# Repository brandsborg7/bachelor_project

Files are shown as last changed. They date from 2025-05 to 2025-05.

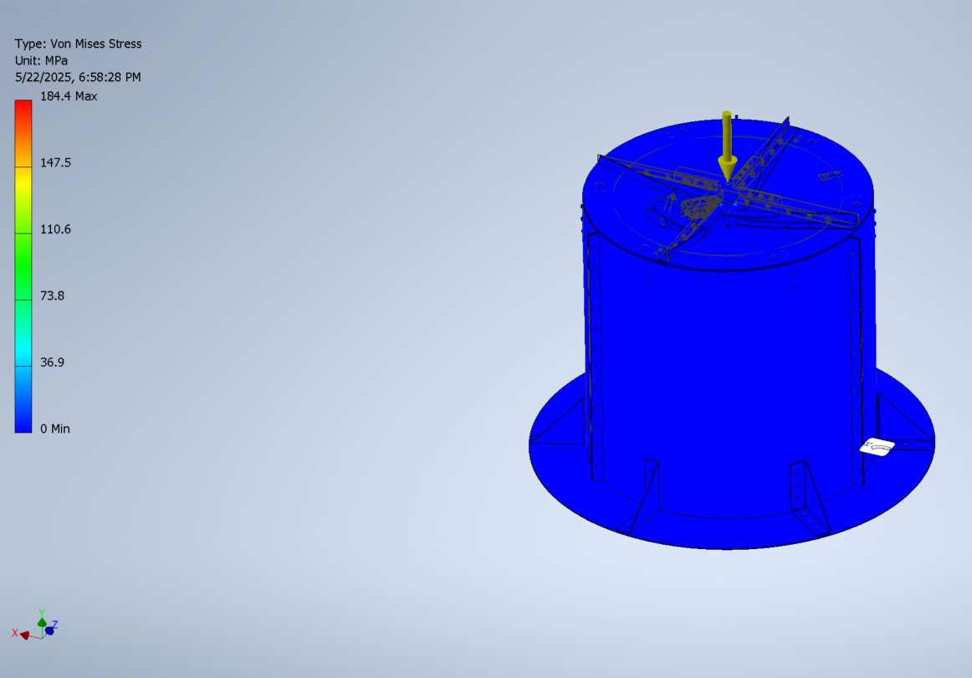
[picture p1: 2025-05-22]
CAD-files/FEA_chamber_results.png

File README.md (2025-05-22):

# bachelor_project
All codes from the workspace on the Raspberry PI of our bachelor project 
NB! Not in the exact way they are represented in the workspace folder on the RPi, but just to illustrate all the codes 
the most efficient way (for the bachelor report) 

Each node-folder has a package.xml, setup.py (used for building the package), as well as the Python code for the node. 

Extra files included: 
- logfile (from last final testings 19th of May)
- Plots/graphs from the sensor data (created by the logger_node as .png files)
- dockerfile.txt & docker-compose.yml (used to create, build & run the Docker environment)
- config.txt file (which is the config file for the Raspberry Pi located in /boot/firmware/config.txt)

Additional: 
- The project's BOM list is included (BOM_våk_field_flux.xlsx)
- All CAD-files (technical drawings) are in the CAD-files folder

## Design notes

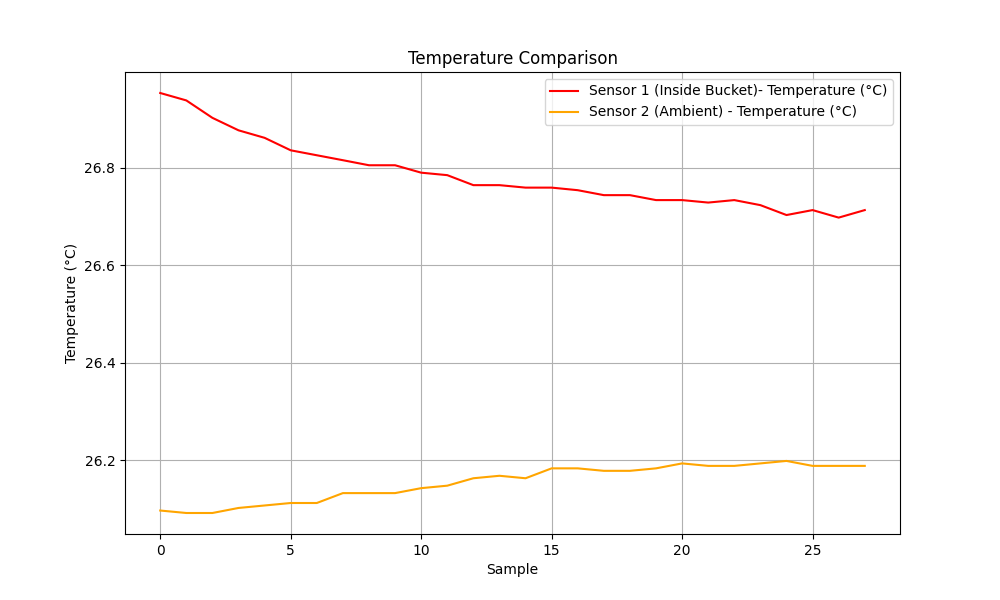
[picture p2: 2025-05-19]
Plots (sensor data)/19.mai/temperature_comparison_2025-05-19_14-41-35.png

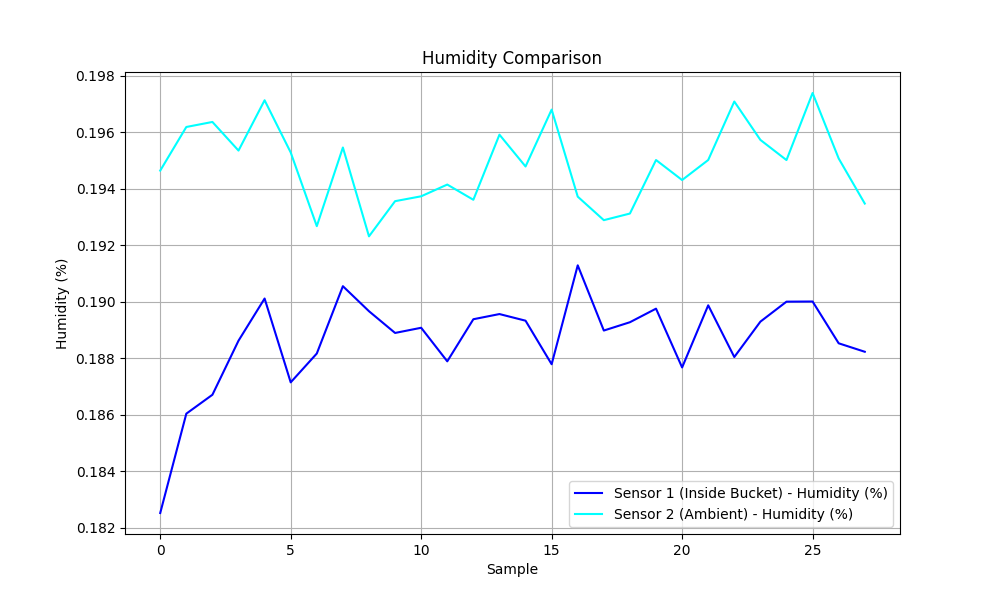
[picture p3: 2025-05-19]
Plots (sensor data)/19.mai/humidity_comparison_2025-05-19_14-41-35.png

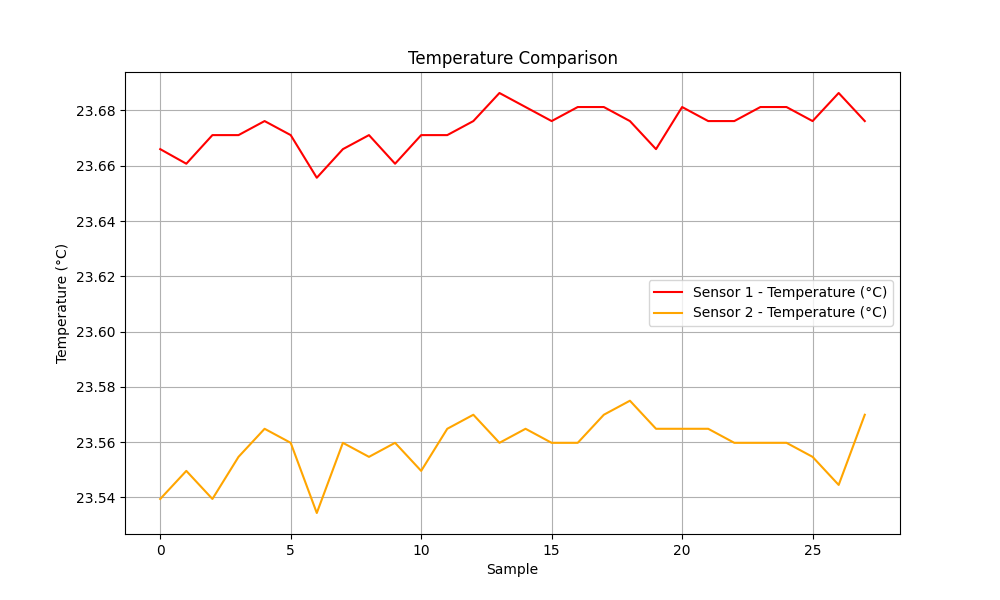
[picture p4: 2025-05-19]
Plots (sensor data)/16.mai/temperature_comparison_2025-05-16_08-13-00.png

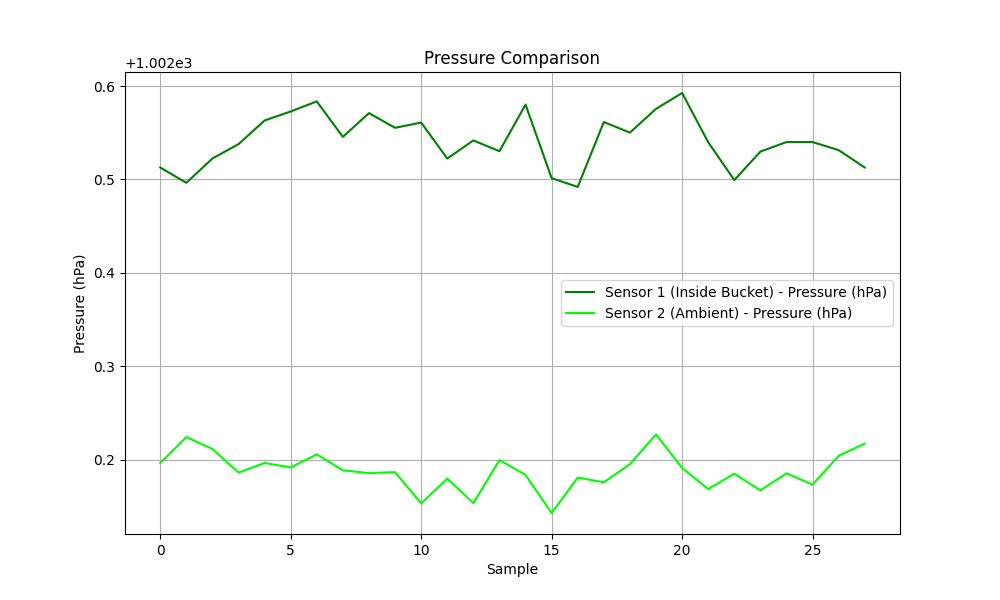
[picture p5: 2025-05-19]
Plots (sensor data)/19.mai/pressure_comparison_2025-05-19_14-41-35.png

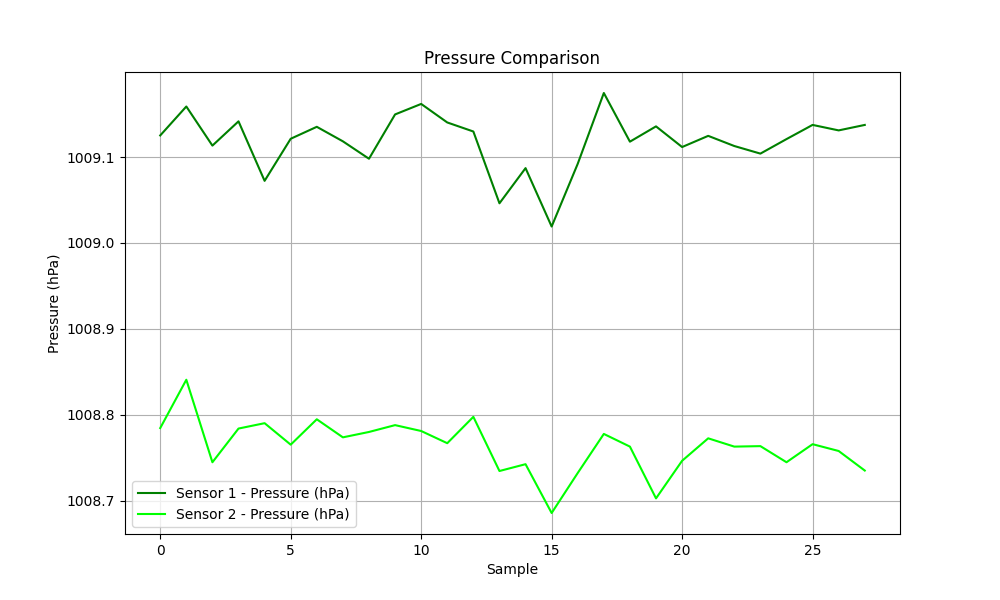
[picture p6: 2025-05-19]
Plots (sensor data)/16.mai/pressure_comparison_2025-05-16_08-13-00.png

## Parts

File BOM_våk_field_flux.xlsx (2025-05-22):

BOM (Bill of Materials)
Electronics / hardware | Quantity | Category | Description / Specifications | Notes | Source / Link
Raspberry Pi 5 | 2 | RPi |  |  | https://no.farnell.com/raspberry-pi/rpi5-4gb-single/raspberry-pi-5-model-b-4gb-2-4ghz/dp/4255998
Rasperry PI case w/cooling fan | 2 | RPi | Protective case w/cooling fan for the RPi 5 |  | https://no.farnell.com/raspberry-pi/sc1160/case-raspberry-pi-5-model-b-plastic/dp/4263048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
Storage: MicroSD m/adapter | 2 | RPi | 128 GB |  | https://no.farnell.com/hama/00124160/128gb-c10-uhs-i-microsdhc-80mb/dp/3410186
Rasperry Pi Power Supply | 1 | RPi | 5V, USB-C |  | https://no.farnell.com/raspberry-pi/sc1152/power-supply-usb-c-5-1v-5a-white/dp/4263039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
Rasperry Pi Motor Driver Board | 1 | RPi | 4A, 24V |  | https://thepihut.com/products/raspberry-pi-motor-driver-board
24V Battery (Power source) | 1 | Power |  | Ended up using the battery already installed in VÅK | Adigo
Mikroswitch (endebryter) | 2 |  |  | Did not end up using them | https://no.farnell.com/omron/z-15g/microswitch-spdt-15a-250vac-solder/dp/3413281 | https://no.mouser.com/ProductDetail/Saia-Burgess/XGC2-88Z1?qs=lDMevKbHVys%2F1Eo18luQHQ%3D%3D | https://no.rs-online.com/web/p/micro-switches/8046225?gb=s
RC Servo | 2 | Bøtte | To open & close lids of bucket |  | https://www.elefun.no/vare-1016/radioutstyr-servo-hitec-hs-322hd
Voltage Regulator | 1 | Power | Step down 24V to 5V (5A output) | Ended up using the voltage regulator already installed the VÅK | https://no.farnell.com/mean-well/sd-25a-5/dc-dc-converter-5v-5a/dp/2816175
Voltage Regulator (VÅK) | 1 | Power | Step down 24V to 5V (5A output) |  | Adigo
Ethernet cable | 2 | Wiring | CAT6 |  | Adigo
DC Axial-fan | 2 | Bøtte | 40 x 40mm, 5V |  | https://no.farnell.com/sepa/lf40p05pse00a/dc-fan-40mm-7500rpm-5v-0-1a/dp/3886338
USB HD-Camera | 2 | Bøtte | 41 mm x 41 mm x 41.5 mm, 5V, 1080p Full HD |  | https://no.mouser.com/ProductDetail/AAEON-UP/EP-DCOV2735-F36?qs=w%2Fv1CP2dgqpCcX2%252BgWo9%2Fg%3D%3D
Male USB A to Female USB A | 2 | Wiring | 480Mbps, 1.8m |  | https://no.rs-online.com/web/p/usb-cables/1862790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
Wires |  | Wiring | 18-22 AWG |  | Adigo
Environmental Sensor | 2 | Bøtte | I2C: temperature, humidity, pressure |  | https://no.farnell.com/en-NO/seeed-studio/101020193/sensor-board-arduino-board/dp/3932095?cfm=true
Våk-robot | 1 |  |  |  | Adigo
Mechanical parts | Quantity | Category | Description / Specifications | Notes | Source / Link
Aluminium til bom | 1 | Bom | 210cm x 4cm x 3cm | Al rør rektang 6060-T6 60x40x3mm a 6000mm (vi trenger totalt 350cm) | Astrup.no
Aluminium til bom | 1 | Bom | 110cm x 4cm x 3cm | Al rør rektang 6060-T6 60x40x3mm a 6000mm (vi trenger totalt 350cm) | Astrup.no
1m aluminiumsrør | 1 | Kobling | 6060-T6 22x2mm | Al rør 6060-T6 22x2mm a 6000mm | Astrup.no
1m aluminiumsrør | 1 | Kobling | 6060-T6 35x2mm | Al rør 6060-T6 35x2mm a 6000mm | Astrup.no
Aluminium-plater | 2 | Bøtte | 2m x 1m x 2mm |  | Astrup.no
Alu vinkelprofil | 1 | Bøtte | 6m (20 x 20 x 2mm) | https://kundeportal.astrup.no/aluminium/alu-vinkler-like-ulikebent | Astrup.no
Wire til festet på bøtta | 1 | Kobling | 3m x 2mm |  | RS PRO Galvanised Metal Wire Rope, 50m | RS (https://no.rs-online.com/web/p/rope/1244758)
3D-print bushing | 4 | Kobling |  |  | Adigo
Clamping knob (til bøtter) | 2 | Bøtte |  |  | RS PRO Clamping Lever, M8 x 40mm | RS (https://no.rs-online.com/web/p/clamping-levers/0478945?matchtype=&gad_source=1&gclsrc=aw.ds)
rivets, aluminium | 3 pcs of 50 units | Bøtte | 5mm |  | RS PRO Aluminium Blind Rivet, 4.8mm | RS (https://no.rs-online.com/web/p/rivets/2065416?gb=a)
Luftslange kobling (siste fase av produksjon) | 2 | Bøtte |  |  | RS PRO Straight Tube-to-Tube Adaptor, Push In 6 mm to Push In 6 mm, Tube-to-Tube Connection Style | RS (https://no.rs-online.com/web/p/pneumatic-fittings/9160873)
Vakuumslange (siste fase av produksjon) |  | Bøtte | 8m x 6mm |  | https://no.rs-online.com/web/p/hose-pipe-flexible-tubes/9145515?gb=s
Endeledd | 2 | Bøtte | M6 45mm |  | RS PRO M6 x 1 Male Steel Rod End, 6mm Bore, 45mm Long, Metric Thread Standard, Male Connection Gender | RS (https://no.rs-online.com/web/p/rod-ends/1989077?gb=s)
Gassfjær 6-15 | 2 | Kobling | 200mm strokelength - Total length: 430 +/- 2mm, 150N |  | Gassfjær 4-12 - slaglengde 150 - Gassfjaershop.no (https://www.gassfjaershop.no/produkt/gassfjaer-4-12-slaglengde-150/)
Neopren | 1 | Bøtte | 1m x 0,6m x 1,5mm |  | Rubber Sheets | RS (https://no.rs-online.com/web/c/engineering-materials-industrial-hardware/plastic-rubber-materials/rubber-sheets/)
M8 theaded insert diameter | 4 | Bøtte | 11mm |  | PSZFON-0830 | POP Steel Tubular Rivet, 10.9mm, M8 thread | RS (https://no.rs-online.com/web/p/rivets/7689984?gb=s)
M5 threaded insert diameter | 8 | Bøtte | 7mm |  | RS PRO Black Multiple Lobes Clamping Knob, M8, Threaded Stud | RS (https://no.rs-online.com/web/p/clamping-knobs/7027633)
Foam | 1 | Bøtte | 10 x 6 x 5000 mm |  | Adigo
Bøjlewirelås DIN741 |  |  | A2 2 mm |  | https://www.globaltools.no/tekniske-artikler/wire-kaeder/-7854/wireklemme-alu-z-20-mm-100-stk
Trådklemme alu-z |  |  | 2,0 mm |  | https://www.globaltools.no/tekniske-artikler/wire-kaeder/-7854/bojlewirelas-din741-a2-2-mm
Poppnagler | 150 |  | 4,8x10 "plain" alu
Source / suppliers:
Astrup.no
Norsk stål
Tverlie sveis (vals og tig)
Takshop.no (vals og tig)
no.farnell.com
https://no.rs-online.com/web/
https://no.farnell.com/
Global Tools
www.gassfjaershop.no

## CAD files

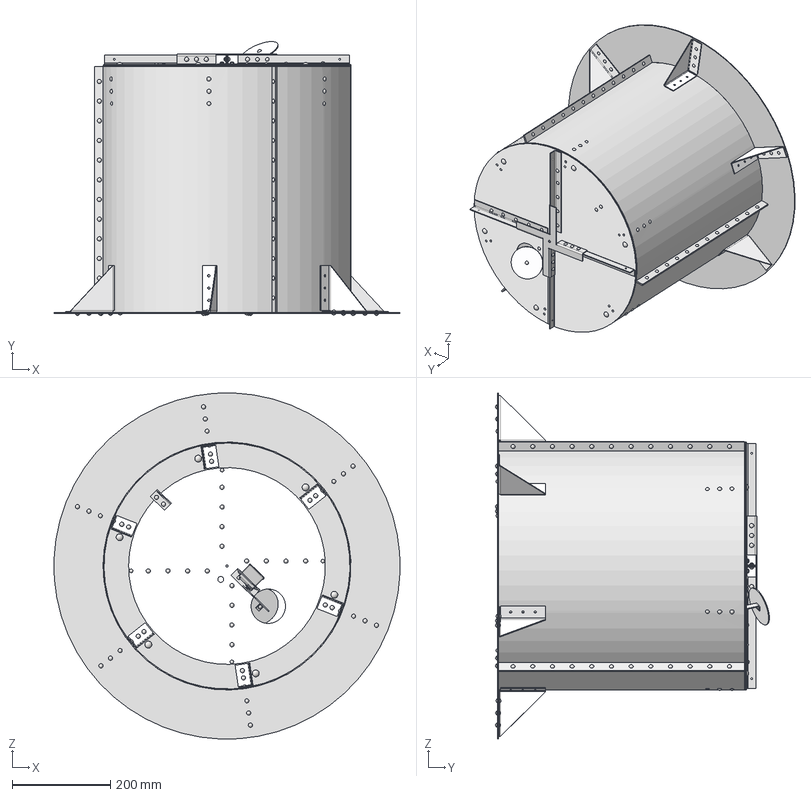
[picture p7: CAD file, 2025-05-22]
CAD-files/assembly_lokk.stp
703.4 x 556.9 x 703.4 mm
Lokk_strut x 4
connector_cross
lufte_lokk
lokk
servofeste
servo_arm
vifte
_HS-322HD
ISO/R 1051 - 5 x 10 x 121
botte_sylinder_tredelt x 3
botte_kant
botte_skjort
botte_skjort_feste x 6
botte_kant_feste x 6
ISO/R 1051 - 8 x 14 x 6

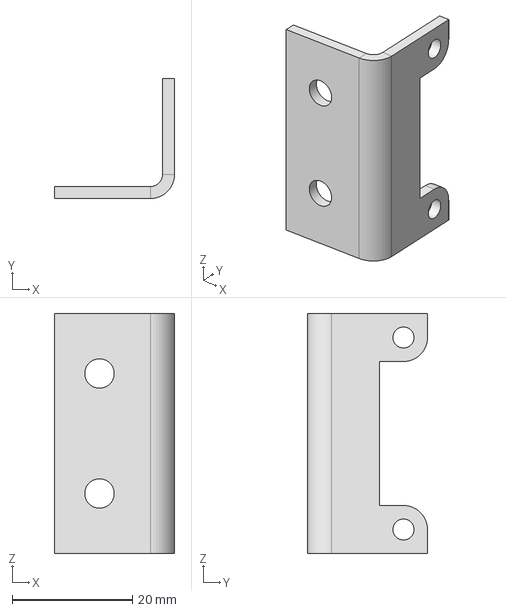
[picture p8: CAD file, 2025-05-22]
CAD-files/vifte.stp
20.0 x 20.0 x 40.0 mm

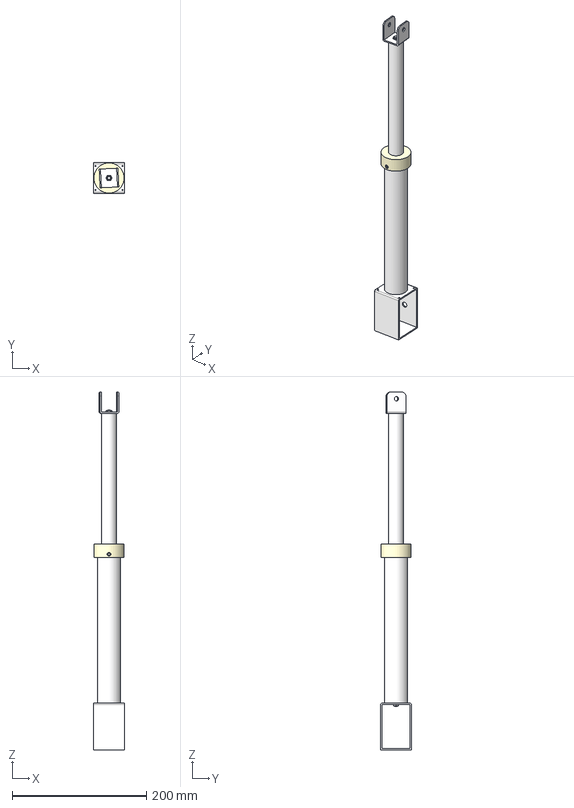
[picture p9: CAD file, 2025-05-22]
CAD-files/Piston damper.stp
46.0 x 46.0 x 534.0 mm
Bushing outer
Ny type indre
Øvre del kobling
Bushing indre kobling
ISO 1207 - M3 x 4 x 2
rod
thread rod
thread cylinder
ISO 4035 - M5 x 2
ISO 1207 - M2,5 x 3 x 2

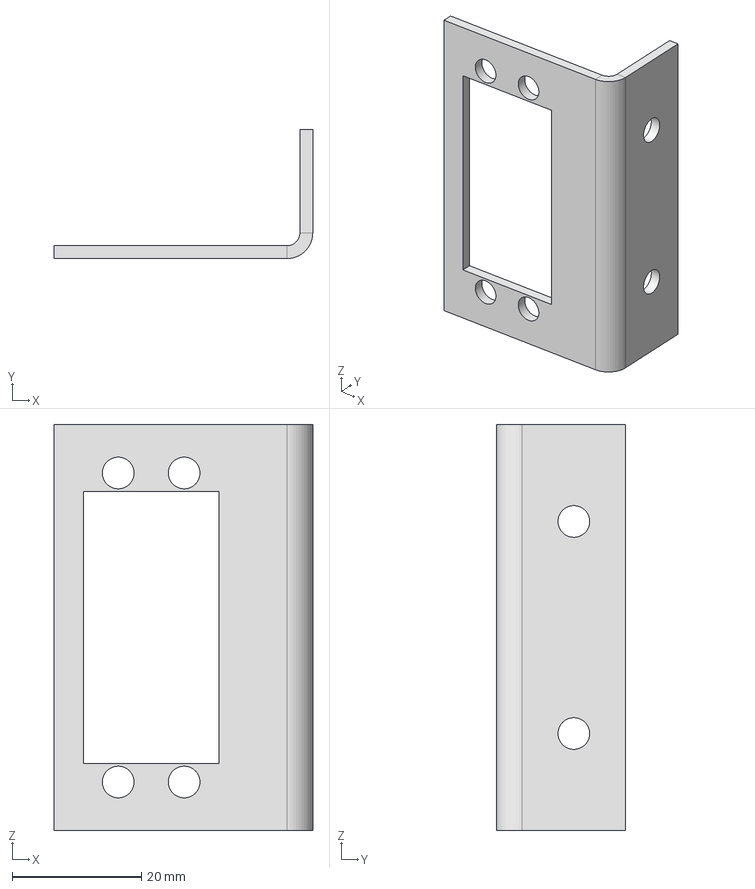
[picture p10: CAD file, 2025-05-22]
CAD-files/servofeste.stp
40.0 x 20.0 x 62.8 mm

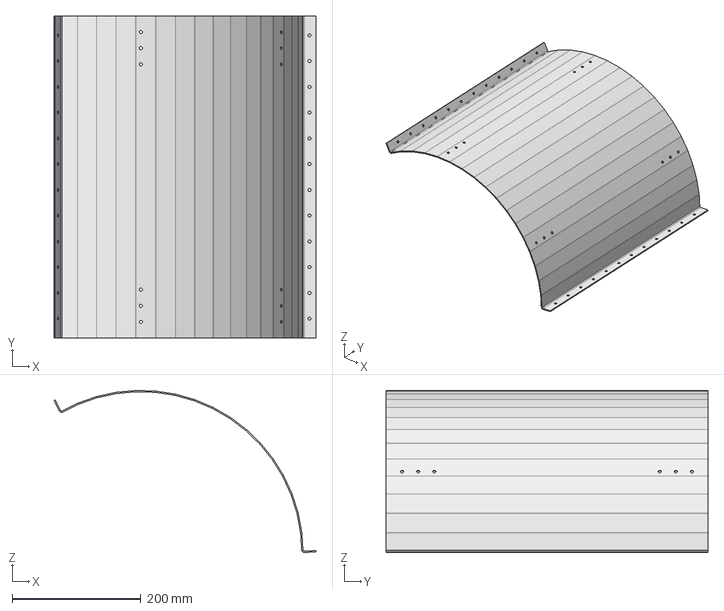
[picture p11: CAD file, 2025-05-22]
CAD-files/botte_sylinder_tredelt_sheet.stp
406.8 x 500.0 x 251.6 mm

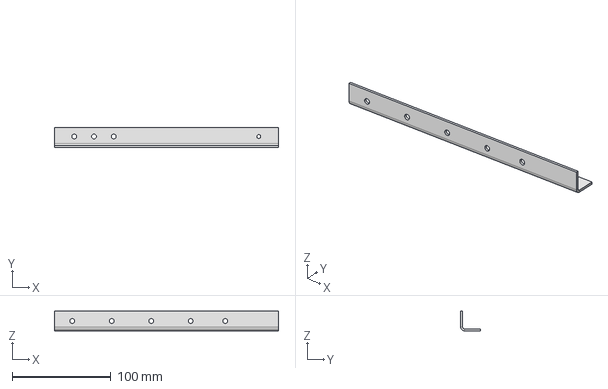
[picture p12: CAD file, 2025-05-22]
CAD-files/Lokk_strut.stp
227.0 x 20.0 x 20.0 mm

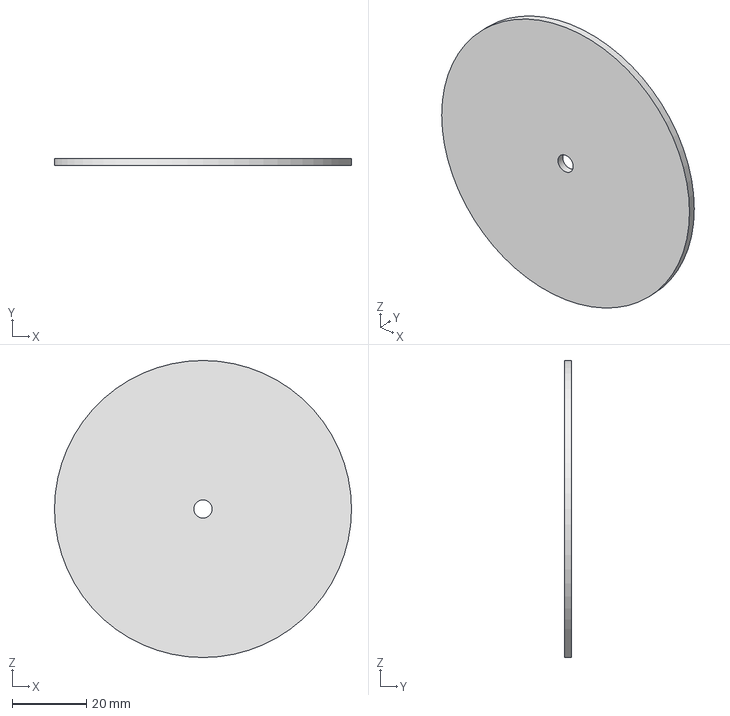
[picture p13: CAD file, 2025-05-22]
CAD-files/lufte_lokk.stp
80.0 x 2.00 x 80.0 mm

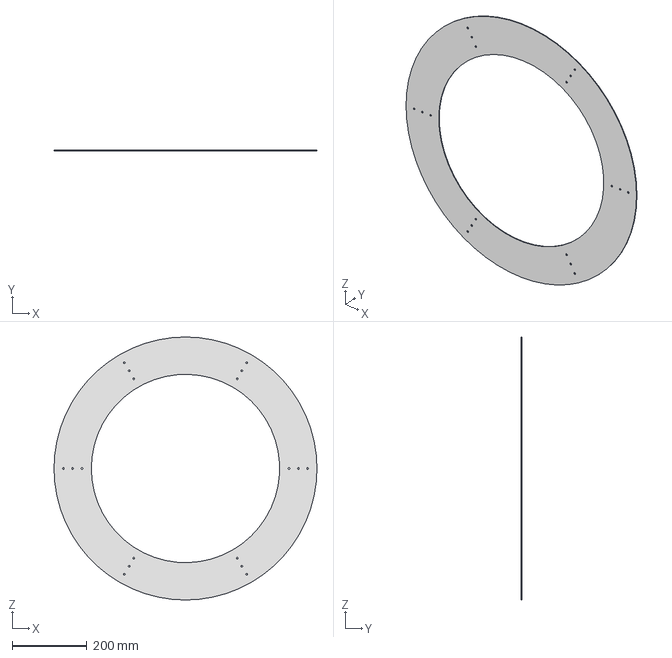
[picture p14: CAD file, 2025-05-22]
CAD-files/botte_skjort.stp
704.0 x 2.00 x 704.0 mm

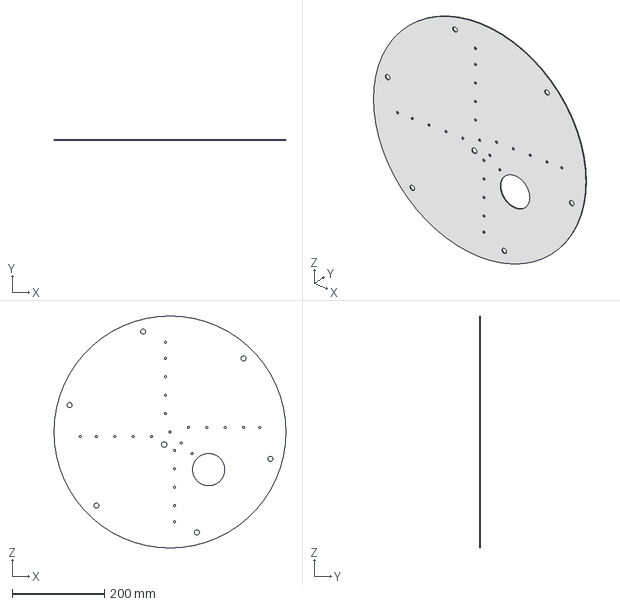
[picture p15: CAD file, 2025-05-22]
CAD-files/lokk.stp
504.0 x 2.00 x 504.0 mm

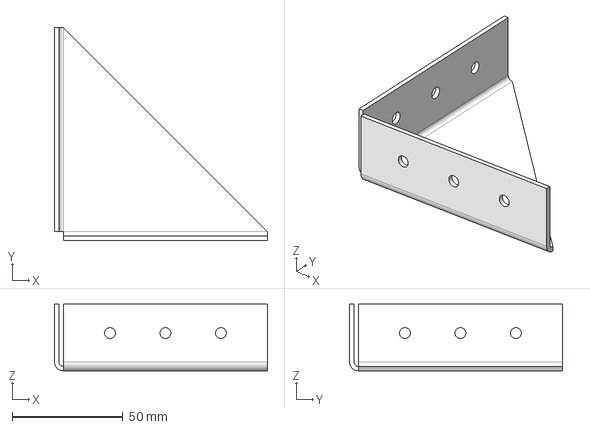
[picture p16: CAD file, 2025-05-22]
CAD-files/botte_skjort_feste.stp
96.0 x 96.0 x 30.0 mm

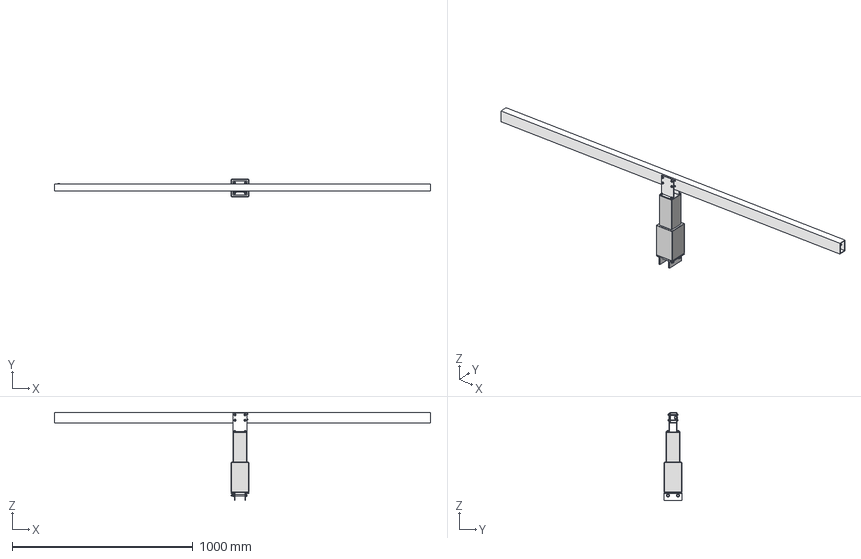
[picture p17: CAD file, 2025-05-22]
CAD-files/Beam and brackets simple.stp
2080.0 x 97.0 x 489.2 mm
Bom_simple
Heis dummy nedre stilling
ISO 7091 - ST 8 - 100 HV x 2
ISO 4034 - M8 x 2
ISO 4762 - M5 x 25 x 4
ISO 4162 - M5 x 50 x 4
ISO 4161 - M5 x 4
Nut GB/T 17880.4-1999 M8 x 15 x 2
Brakett nedre x 2
ISO 4162 - M8 x 80 x 2
Bom brakett øvre x 2

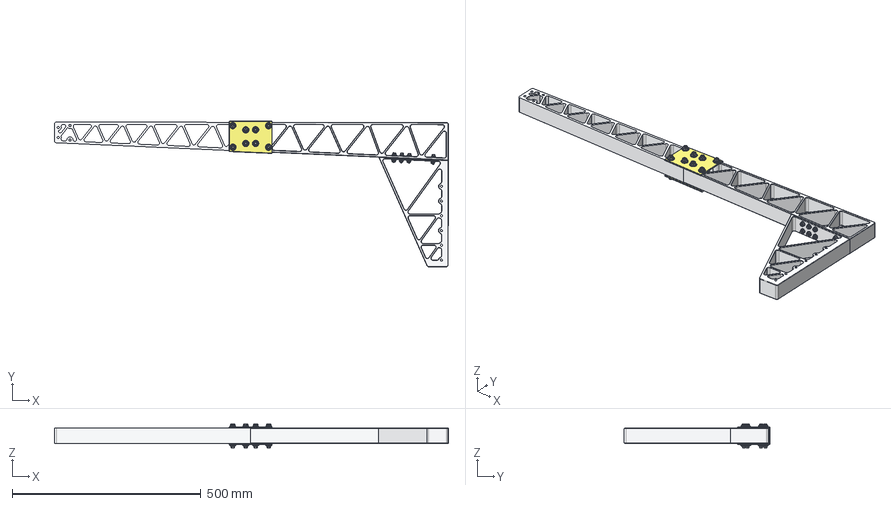
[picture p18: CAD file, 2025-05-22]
CAD-files/Framework.stp
1042.5 x 385.6 x 63.2 mm
Bom_fag_øvre
Bom_fag_nedre
IFI - 5, RTW x 16
IFI 502 - M5x0,8 x 20, HFHTSTDM x 8
ANSI B18.2.4.4M - M5 x 0,8 x 8
Bom_brakett
IFI - 6, RTW x 16
IFI 536 - M6x1 x 55, HFSM x 8
ANSI B18.2.4.4M - M6 x 1 x 8

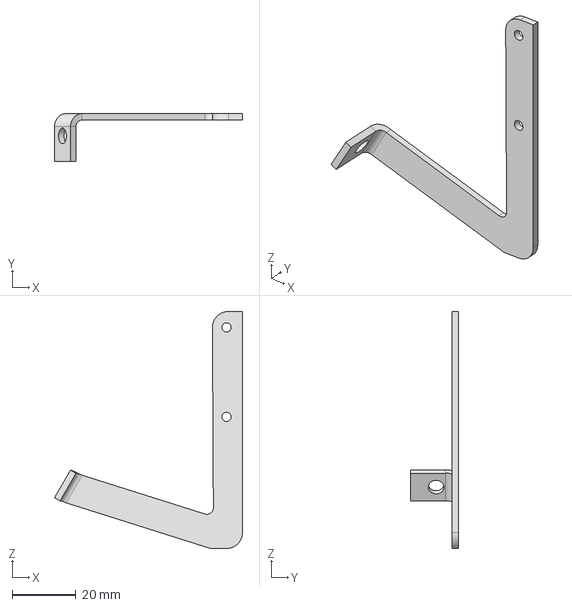
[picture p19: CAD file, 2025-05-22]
CAD-files/servo_arm.stp
58.9 x 15.0 x 74.2 mm

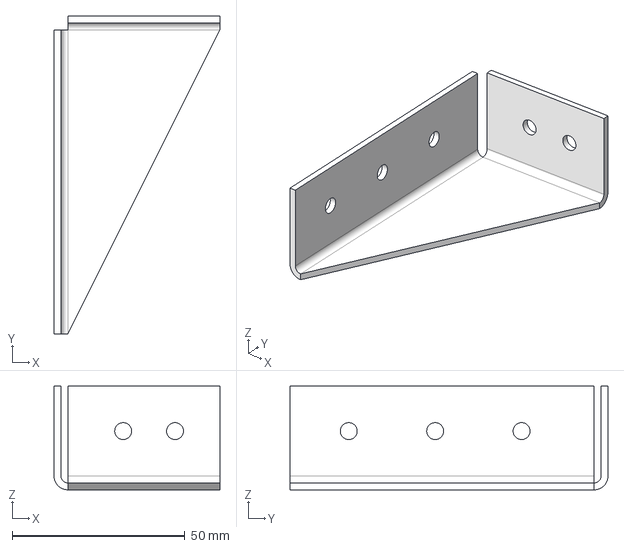
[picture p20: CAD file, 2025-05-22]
CAD-files/botte_kant_feste.stp
48.0 x 92.0 x 30.0 mm

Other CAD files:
CAD-files/connector_cross.stp
CAD-files/botte_kant.stp

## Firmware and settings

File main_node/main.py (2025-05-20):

import rclpy
from rclpy.node import Node
from rclpy.executors import MultiThreadedExecutor
from std_msgs.msg import String
import time
import threading

# Importing necessary modules for the main node
from lift_node.lift import LiftNode
from sensor_node.sensor import SensorPublisher
from rc_servo_node.rc_servo import RCServoNode
from fan_node.fan import FanNode
from camera_node.camera import CameraNode

class MainNode(Node):
    def __init__(self):
        super().__init__('main_node')

        # Log the node startup using ROS 2 logger
        self.get_logger().info("Main Node has been started")

        # Initial variable conditions
        self.running = True
        self.shutdown_everything = False
        self.lift_in_stopped_condition = True
        self.lift_sequence_phase = None
        self.sequence_active = False

        # Initialize the nodes (with error handling)
        self.lift_node = self.safe_init(LiftNode)
        self.sensor_node = self.safe_init(SensorPublisher)  
        self.rc_servo_node = self.safe_init(RCServoNode)
        self.fan_node = self.safe_init(FanNode)
        self.camera1_node = self.safe_init(CameraNode, 0)
        self.camera2_node = self.safe_init(CameraNode, 2)
        
        # Publishers
        self.lift_cmd_publisher = self.create_publisher(String, 'lift_cmd', 10) # lift_cmd topic
        self.shutdown_pub = self.create_publisher(String, 'shutdown_topic', 10) # shutdown_topic

        # Lift status subscriber (for sequence control)
        self.lift_status_sub = self.create_subscription(String, 'lift_status', self.lift_status_callback, 10)

    # Function to safely initialize nodes (w/its arguments and keyword-arguments) and handle exceptions
    def safe_init(self, class_name, *args, **kwargs):
        try:
            return class_name(*args, **kwargs)
        except Exception as e:
            self.get_logger().error(f"Failed to initialize {class_name.__name__}: {e}")
            return None

    # Function to send shutdown message to the logger node
    def shutdown_logger(self):
        msg = String()
        msg.data = 'shutdown'
        self.shutdown_pub.publish(msg)
        self.get_logger().info('Sendt shutdown message to logger_node.')

    def send_lift_command(self, command: str):
        try:
            msg = String()
            msg.data = command
            self.lift_cmd_publisher.publish(msg)
            self.get_logger().info(f"Sent command: {command}")
        except Exception as e:
            self.get_logger().error(f"Failed to send lift command: {e}, command: {command}")

    def shutdown_nodes(self):

        # Stop the command loop
        self.running = False

        nodes_to_shutdown = [
            self.lift_node,
            self.sensor_node,
            self.rc_servo_node,
            self.fan_node,
            self.camera1_node,
            self.camera2_node,
        ]

        for node in nodes_to_shutdown:
            if node:
                try:
                    node_name = node.get_name()
                    node.destroy_node()
                    self.get_logger().info(f"Node {node_name} has been destroyed.")
                except Exception as e:
                    self.get_logger().error(f"Failed to destroy node: {e}")
            else:
                self.get_logger().warn("Node is None, skipping destruction.")
        
        self.get_logger().info("Main node shutting down.")

    # Function to start multiple threads simultaneously (just starting them)
    def start_threads(self, funcs):
        threads = []
        for f in funcs:
            thread = threading.Thread(target=f)
            thread.start()
            threads.append(thread)
        return threads
    
    def run_thread_and_wait(self, funcs):
        threads = self.start_threads(funcs)
        for thread in threads:
            thread.join()

    def lift_status_callback(self, msg):
        status = msg.data
        self.get_logger().info(f"Received lift status: {status}")

        # Only handle lift status when in full sequence
        if not self.sequence_active:
            return

        if status == "Lift stopped":

            # Step 5: Close the LIDs (servos), turn off fans 
            if self.sequence_phase == 1:   # Lift down just finished (STOPPED)
                

                if self.rc_servo_node:
                    self.run_thread_and_wait([
                    lambda: self.rc_servo_node.servo_1.process_command("close"),
                    lambda: self.rc_servo_node.servo_2.process_command("close"),
            ])

                self.get_logger().info("Lift down completed. Closing servos.")
                
                self.get_logger().info("Servos closed. Turning off fans.")
                self.fan_node.turn_off_fans()

                # Step 6: Lift up
                if self.lift_node:
                    self.lift_node.lift_up(duration=40)
                self.sequence_phase = 2

            # Step 7 (final): stop the sequence & turn off cameras
            elif self.sequence_phase == 2:  # Lift up just finished (STOPPED)
                # Lift up just finished
                self.get_logger().info("Lift up completed. Turning off cameras")
                
                # Stop the cameras 
                for thread in self.camera_threads:
                    thread.join()

                self.lift_in_stopped_condition = True
                self.sequence_phase = None
                self.sequence_active = False 
                self.get_logger().info("Full sequence completed.")

    def full_sequence(self): 
        self.get_logger().info("Starting full sequence...")

        if not all([self.lift_node, self.fan_node, self.rc_servo_node]):
            self.get_logger().error("❌ One or more required nodes are not initialized. Aborting sequence.")
            return

        if not self.lift_in_stopped_condition:
            self.get_logger().warn("⚠️ Lift is currently moving. Wait for it to stop before running sequence.")
            return
        
        self.sequence_active = True  # Sequence is now active

        try: 

            # Step 1: Start camera recordings 
            self.get_logger().info("🎥 Starting camera recordings (100s)...")
            self.camera_threads = self.start_threads([
                lambda: self.camera1_node.create_video(100),
                lambda: self.camera2_node.create_video(100),
            ])

            # STEP2: Open the LIDs w/servos 
            self.get_logger().info("🔓 Opening servos...")
            self.run_thread_and_wait([
                    lambda: self.rc_servo_node.servo_1.process_command("open"),
                    lambda: self.rc_servo_node.servo_2.process_command("open"),
                    ])
            self.get_logger().info("✅ Servos opened.")

            # Step 3: Lift down 
            self.get_logger().info("⬇️ Lowering lift and turning on fans...")
            self.lift_in_stopped_condition = False # Lift moving 
            self.lift_node.lift_down(duration=40)
            self.sequence_phase = 1  # So that it will go to next phase when lift stops 
            
            # Step 4: Turn on fans
            self.fan_node.turn_on_fans() # Turn on the fans 
            self.get_logger().info("💨 Fans turned on. Waiting for lift to stop...")
        except Exception as e:
            self.get_logger().error(f"❌ Error during full sequence: {e}")
            self.sequence_active = False
            self.sequence_phase = None
 
    def exit(self):
        self.get_logger().info("Exiting main node.")

        # Turn off fans and servos
        if self.fan_node: self.fan_node.shutdown()
        if self.rc_servo_node: self.rc_servo_node.shutdown()

        self.running = False            # This will stop the command loop
        self.shutdown_everything = True
        self.shutdown_logger()
        rclpy.shutdown()
  
    # Loop for command input 
    def run_command_loop(self):
        while rclpy.ok() and self.running:
            try:
                command = input("Enter command (e.g. lift_up, lift_down, lift_stop, lift_test, " \
                "fans_on, rc_test, rc_open, rc_close, cam_test, run_all, exit): ")

                if command == "lift_up": self.send_lift_command("lift_up")
                elif command == "lift_down": self.send_lift_command("lift_down")
                elif command == "lift_stop":
                    self.send_lift_command("lift_stop")
                    self.lift_in_stopped_condition = True
                elif command == "lift_test": self.send_lift_command("lift_test")
                elif command == "fans_on": self.fan_node.turn_on_fans()
                elif command == "rc_test":
                    # Test both servos by opening and closing them (at the same time using threads)
                    self.run_thread_and_wait([
                        lambda: self.rc_servo_node.servo_1.process_command("open"),
                        lambda: self.rc_servo_node.servo_2.process_command("open"),
                    ])

                    # Wait for 1 second before closing the servos 
                    time.sleep(1)  
                    self.run_thread_and_wait([
                        lambda: self.rc_servo_node.servo_1.process_command("close"),
                        lambda: self.rc_servo_node.servo_2.process_command("close"),
                    ])
        
                elif command == "rc_open":
                    self.run_thread_and_wait([
                        lambda: self.rc_servo_node.servo_1.process_command("open"),
                        lambda: self.rc_servo_node.servo_2.process_command("open"),
                    ])
                elif command == "rc_close":
                    self.run_thread_and_wait([
                        lambda: self.rc_servo_node.servo_1.process_command("close"),
                        lambda: self.rc_servo_node.servo_2.process_command("close"),
                    ])
                elif command == "cam_test":
                    self.get_logger().info("Starting camera test (5 seconds)...")

                    self.run_thread_and_wait([
                        lambda: self.camera1_node.create_video(5),
                        lambda: self.camera2_node.create_video(5),
                    ])

                    self.get_logger().info("Camera test completed.")
                elif command == "run_all": self.full_sequence()
                elif command == "exit": 
                    self.exit()
                    break
                else:
                    self.get_logger().info(f"Unknown command: {command}")
                
                print("Command completed. Enter a new command:\n")

            except KeyboardInterrupt:
                        self.get_logger().info("Main node interrupted by keyboard")
                        self.running = False
                        break

def main(args=None):

    # Initialize to None to avoid reference before assignment
    main_node = None    
    executor = None     
    command_thread = None  

    try:
        rclpy.init(args=args)  # Initialize the ROS 2 context
        main_node = MainNode()

        # MultiThreadedExecutor that spins all nodes in separate threads
        executor = MultiThreadedExecutor()
        executor.add_node(main_node)  # Add the main node to the executor

        # Add all the child nodes to the executor (if they are not None)
        for node in [main_node.lift_node, main_node.rc_servo_node, main_node.fan_node, 
                     main_node.camera1_node, main_node.camera2_node]:
            if node:
                executor.add_node(node)

        # Add the sensor node only if at least one sensor is available
        if main_node.sensor_node.sensor1 or main_node.sensor_node.sensor2:
            executor.add_node(main_node.sensor_node)
        else:
            main_node.get_logger().warn("One or both sensors are not available, skipping addition to executor.")
        
        # Start the command loop in a separate thread (to avoid blocking the executor)
        command_thread = threading.Thread(target=main_node.run_command_loop, daemon=True)
        command_thread.start()

        # Spin all the nodes in the executor
        executor.spin()

    except KeyboardInterrupt:
        if main_node:
            main_node.get_logger().info("Main node interrupted by user")

    except Exception as e:
        if main_node:
            main_node.get_logger().error(f"Unexpected error occurred in main node: {e}")

    finally:

        if main_node and main_node.shutdown_everything:

            if executor:
                executor.shutdown()  # Shutdown the executor properly

            if main_node:
                main_node.shutdown_nodes()  # Shutdown all nodes
                main_node.destroy_node()

            # Wait for the command thread to finish        
            if command_thread and command_thread.is_alive():
                try: 
                    command_thread.join()
                except RuntimeError:
                    if main_node:
                        main_node.get_logger().error("[RuntimeError]: Error while waiting for command thread to finish.")

            if rclpy.ok():
                rclpy.shutdown()
if __name__ == '__main__':
    main()

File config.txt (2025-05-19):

# For more options and information see
# http://rptl.io/configtxt
# Some settings may impact device functionality. See link above for details

# Uncomment some or all of these to enable the optional hardware interfaces

# SET I2C = ON
#dtparam=i2c_arm=on
#dtparam=i2s=on
#dtparam=spi=on

# Enable audio (loads snd_bcm2835)
dtparam=audio=on

# Additional overlays and parameters are documented
# /boot/firmware/overlays/README

# Automatically load overlays for detected cameras
camera_auto_detect=1

# Automatically load overlays for detected DSI displays
display_auto_detect=1

# Automatically load initramfs files, if found
auto_initramfs=1

# Enable DRM VC4 V3D driver
dtoverlay=vc4-kms-v3d
max_framebuffers=2

# Don't have the firmware create an initial video= setting in cmdline.txt.
# Use the kernel's default instead.
disable_fw_kms_setup=1

# Run in 64-bit mode
arm_64bit=1

# Disable compensation for displays with overscan
disable_overscan=1

# Run as fast as firmware / board allows
arm_boost=1

[cm4]
# Enable host mode on the 2711 built-in XHCI USB controller.
# This line should be removed if the legacy DWC2 controller is required
# (e.g. for USB device mode) or if USB support is not required.
otg_mode=1

[cm5]
dtoverlay=dwc2,dr_mode=host

[all]

# FANS

# Set GPIO23 to low at boot
dtoverlay=gpio,gpiopin=23,active_low=1

# Set GPIO24 to low at boot
dtoverlay=gpio,gpiopin=24,active_low=1

# RC-SERVOS

# Set GPIO18 to low at boot
dtoverlay=gpio,gpiopin=18,active_low=1

# Set GPIO25 to low at boot
dtoverlay=gpio,gpiopin=25,active_low=1

# Enable SPI
dtparam=spi=on

# Enable UART0 
dtparam=uart0=on

# Enable I2C
dtparam=i2c_arm=on

# Extra I2C-bus på BUS3 on GPIO0 (IDSD) and GPIO1 (IDSC)
dtoverlay=i2c-gpio,bus=0,i2c_gpio_sda=0,i2c_gpio_scl=1

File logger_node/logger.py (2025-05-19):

# ROS2 Communication Libraries
import rclpy
from rclpy.node import Node
from sensor_msgs.msg import Temperature, RelativeHumidity, FluidPressure
from std_msgs.msg import String, Bool

# Libraries for logging, plotting and file handling 
import time
import logging 
import os
import matplotlib.pyplot as plt
from datetime import datetime

class LoggerNode(Node):
    def __init__(self):
        super().__init__('logger_node')

        # Set up path to the log_file 
        log_dir = '/media/pi/ELLAB/bachelor_prosjekt/ros2_logs/'


        try: 
            os.makedirs(log_dir, exist_ok=True)  # Create the folder if it doesn't already exist
        except Exception as e:
            self.get_logger().error(f"Failed to create log directory: {e}")
            return
          
        log_file = os.path.join(log_dir, f'log_{datetime.now().strftime("%Y%m%d_%H%M%S")}.log')

        # Configure the logger to both log to terminal and to file
        self.logger = logging.getLogger('LoggerNode')
        self.logger.setLevel(logging.INFO)

        # Terminal-handler for logging to terminal
        console_handler = logging.StreamHandler()
        console_handler.setLevel(logging.INFO)
        formatter = logging.Formatter('%(asctime)s - %(message)s')
        console_handler.setFormatter(formatter)
        self.logger.addHandler(console_handler)

        # Filehandler for logging 
        file_handler = logging.FileHandler(log_file)
        file_handler.setLevel(logging.INFO)
        file_handler.setFormatter(formatter)
        self.logger.addHandler(file_handler)

        self.logger.info("Logger Node has been started")
        self.logger.info("----------------------------")

        # Shutdown flag 
        self.shutdown_flag = False

        # Subscriber for shutdown message (from main node)
        self.shutdown_subscriber = self.create_subscription(
            String,
            'shutdown_topic',
            self.shutdown_callback,
            10
        )

        # Buffer lists for saving values 
        self.sensor_1_temp_list = []
        self.sensor_1_humidity_list = []
        self.sensor_1_pressure_list = []

        self.sensor_2_temp_list = []
        self.sensor_2_humidity_list = []
        self.sensor_2_pressure_list = []

        # Subscribers for sensor 1
        self.create_subscription(Temperature, 'sensor1/temperature', self.temp_callback_1, 10)
        self.create_subscription(RelativeHumidity, 'sensor1/humidity', self.humidity_callback_1, 10)
        self.create_subscription(FluidPressure, 'sensor1/pressure', self.pressure_callback_1, 10)

        # Subscribers for sensor 2
        self.create_subscription(Temperature, 'sensor2/temperature', self.temp_callback_2, 10)
        self.create_subscription(RelativeHumidity, 'sensor2/humidity', self.humidity_callback_2, 10)
        self.create_subscription(FluidPressure, 'sensor2/pressure', self.pressure_callback_2, 10)

        # Subscriber for lift status
        self.create_subscription(String, 'lift_status', self.lift_status_callback, 10)

        # [2 x RC-SERVO] Subscriber for RC-servo (lid) status
        self.create_subscription(String, 'rc_servo_1_status', self.rc_servo_1_status_callback, 10)
        self.create_subscription(String, 'rc_servo_2_status', self.rc_servo_2_status_callback, 10)

        # [2 x FAN] Subscriber for fan status
        self.create_subscription(String, 'fan_1_status', self.fan_1_status_callback, 10)
        self.create_subscription(String, 'fan_2_status', self.fan_2_status_callback, 10)   

        # [2 x camera] subscriber for camera status
        self.create_subscription(Bool, 'camera0_status', self.camera_1_status_callback, 10)
        self.create_subscription(Bool, 'camera2_status', self.camera_2_status_callback, 10)

        # Initialize flags to check if the statuses have been logged initially
        self.logged_camera_1_status = False
        self.logged_camera_2_status = False

        # For storing sensor data for later printing
        self.sensor_1_data = []
        self.sensor_2_data = []

        # Saving timestamps for the plot
        self.timestamps = []

        # For storing lift & servo status & fan status
        self.lift_status = ""
        self.rc_servo_1_status = ""
        self.rc_servo_2_status = ""
        self.fan_1_status = ""
        self.fan_2_status = ""

        # Storing camera status
        self.camera_1_status = False
        self.camera_2_status = False

        # Connection flags
        self.sensor_1_connected = False
        self.sensor_2_connected = False
        self.lift_connected = False
        self.rc_servo_1_connected = False
        self.rc_servo_2_connected = False
        self.fan_1_connected = False
        self.fan_2_connected = False

        # Store timestamps to check if messages are not coming in within a certain time
        self.last_sensor_1_msg_time = time.time()
        self.last_sensor_2_msg_time = time.time()
        self.last_lift_status_time = time.time()
        self.last_rc_servo_1_status_time = time.time()
        self.last_rc_servo_2_status_time = time.time()
        self.last_fan_1_status_time = time.time()
        self.last_fan_2_status_time = time.time()

        # Timeout threshold for checking connections
        self.timeout_threshold = 2  # seconds

    def update_sensor_connection(self, sensor_id):
        if sensor_id == 1:
            self.sensor_1_connected = True
            self.last_sensor_1_msg_time = time.time() # Reset the timer

        elif sensor_id == 2:
            self.sensor_2_connected = True
            self.last_sensor_2_msg_time = time.time()

    def temp_callback_1(self, msg):
        self.sensor_1_temp_list.append(msg.temperature)
        self.sensor_1_data.append(f"Sensor 1 - Temperature: {msg.temperature:.2f} °C")
        self.update_sensor_connection(1)
        self.print_sensor_data()

    def humidity_callback_1(self, msg):
        self.sensor_1_humidity_list.append(msg.relative_humidity)
        self.sensor_1_data.append(f"Sensor 1 - Humidity: {msg.relative_humidity:.2f} %")
        self.update_sensor_connection(1)
        self.print_sensor_data()

    def pressure_callback_1(self, msg):
        self.sensor_1_pressure_list.append(msg.fluid_pressure)
        self.sensor_1_data.append(f"Sensor 1 - Pressure: {msg.fluid_pressure:.2f} hPa")
        self.update_sensor_connection(1)
        self.print_sensor_data()

    def temp_callback_2(self, msg):
        self.sensor_2_temp_list.append(msg.temperature)
        self.sensor_2_data.append(f"Sensor 2 - Temperature: {msg.temperature:.2f} °C")
        self.update_sensor_connection(2)
        self.print_sensor_data()

    def humidity_callback_2(self, msg):
        self.sensor_2_humidity_list.append(msg.relative_humidity)
        self.sensor_2_data.append(f"Sensor 2 - Humidity: {msg.relative_humidity:.2f} %")
        self.update_sensor_connection(2)
        self.print_sensor_data()
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

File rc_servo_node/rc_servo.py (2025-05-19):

# ROS2 Libraries
import rclpy
from rclpy.node import Node
from std_msgs.msg import String

# GPIO control
from gpiozero import Servo
from time import sleep

class RCServo:
    def __init__(self, pin, publisher, logger, name="rc_servo",
                 open_value=-0.5, close_value=0.2, release_after_move=True):
        self.servo = Servo(pin, min_pulse_width=900/1_000_000, max_pulse_width=2100/1_000_000)
        self.publisher = publisher
        self.logger = logger
        self.name = name
        self.open_value = open_value
        self.close_value = close_value
        self.release_after_move = release_after_move

        self.servo.value = None  # Avoid holding on boot
        self.publish_status("closed")

    def process_command(self, command):
        if command == "open":
            self.move_to(self.open_value, "open")
        elif command == "close":
            self.move_to(self.close_value, "closed")
        else:
            self.logger.warning(f"[{self.name}] Unknown command: {command}")

    def move_to(self, target_position, status_label):
        try:
            self.logger.info(f"[{self.name}] Moving to {status_label} (value={target_position})")
            self.servo.value = target_position
            sleep(0.25)  
            if self.release_after_move:
                self.servo.value = None  # Release control after move
            self.publish_status(status_label)
        except Exception as e:
            self.logger.error(f"[{self.name}] Error moving servo: {e}")

    def publish_status(self, status):
        msg = String()
        msg.data = status
        self.publisher.publish(msg)


class RCServoNode(Node):
    def __init__(self):
        super().__init__('rc_servo_node')
        self.get_logger().info("RC Servo Node started")

        # Publishers for each servo's status
        self.servo_1_pub = self.create_publisher(String, 'rc_servo_1_status', 10)
        self.servo_2_pub = self.create_publisher(String, 'rc_servo_2_status', 10)

        # RCServo instances with specific open/close values per servo
        self.servo_1 = RCServo(18, self.servo_1_pub, self.get_logger(), name="rc_servo_1",
                               open_value=-0.5, close_value=0.2, release_after_move=True)
        self.servo_2 = RCServo(25, self.servo_2_pub, self.get_logger(), name="rc_servo_2",
                               open_value=0.15, close_value=0.5, release_after_move=True)

        # Subscribers for each servo commands
        self.create_subscription(String, 'rc_servo_1_command', self.rc_servo_1_callback, 10)
        self.create_subscription(String, 'rc_servo_2_command', self.rc_servo_2_callback, 10)

    def rc_servo_1_callback(self, msg):
        self.servo_1.process_command(msg.data.lower())

    def rc_servo_2_callback(self, msg):
        self.servo_2.process_command(msg.data.lower())

    def shutdown(self):
        self.get_logger().info("Closing the RC-Servos...")

        # Move servos to "closed" position and release control
        self.servo_1.process_command("close")
        self.servo_2.process_command("close")

        self.servo_1.servo.value = None
        self.servo_2.servo.value = None

        try:
            self.servo_1.servo.close()
            self.servo_2.servo.close()
        except Exception as e:
            self.get_logger().warn(f"Error while closing servo GPIO: {e}")
